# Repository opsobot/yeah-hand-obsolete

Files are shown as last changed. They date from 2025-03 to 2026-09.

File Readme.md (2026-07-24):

Yeah Hand (Rebelia V2) - An Open Source Robotic Hand for Humans and Robots
==========================================================================
**Official development partner: Public Invention** [Public Invention Project Page](https://www.pubinv.org/project/yeah-robotic-hand/)



**Original design by Vittorio Lumare** [Hackaday Project Page](https://hackaday.io/project/204373)

**Successor to OSHWA-certified [Rebelia V1](https://github.com/OPSOBOT/rebelia/tree/V1)**

Licenses: 
- CERN-OHL-S-2.0 (Hardware)
- GNU GPLV3 (Software)
- CC-BY-SA (Documentation)

Contributing
------------
- Original hardware, software and documentation by Vittorio Lumare
- Code contributions via Pull Requests to OPSOBOT/yeah-hand
- Public Invention: Official development partner
- All contributions under CERN-OHL-S-2.0 (Hardware), GNU GPL (Software), CC-BY-SA (Docs)

Overview
========

Welcome to the Yeah Hand Project — an open-source, humanlike robotic hand designed for researchers, students, and robotics enthusiasts.

Our goal is to provide an affordable, high-performance robotic hand under 2000 EUR, open to community contributions and continuous improvement.

NOTE: This version will be certified with OSHWA after is stable, at the moment the only version certified with OSHWA is the V1, you can check its branch 'V1' in the repo.

This project hardware is released under the CERN Open Hardware License (OHL-S), ensuring the design remains open-source and preventing patent claims on its core innovations.

The firmware is released under the GNU-GPL License.

The documentation is released under the CC-BY-SA License.

Features
* Fully 3D-printable design using affordable materials.
* Commercial off-the-shelf components for servos and electronics.
* Custom firmware for precise motor control.
* Modularity for easy upgrades and customization.

Our Approach to Open-Source Release
===================================
We use a copyleft open-source license to protect user freedoms and encourage meaningful collaboration, while maintaining a sustainable business model. Our strategy is as follows:

1. Development and Testing: We begin by developing and rigorously testing a new version of our product (including source code, CAD files, documentation, etc.) to ensure it meets our quality and performance standards.

2. Preparation for Launch and Sales: Once the new version is stable, we prepare it for market with dedicated marketing and pre-sales efforts. This phase ensures visibility and early adoption by our community and customers.

3. Open-Source Copyleft Release: We release each version immediately under a copyleft license (e.g., CERN-OHL, GPL), ensuring that the community can study, modify, and share the design—while also preserving those freedoms in derivative works. At the same time, we begin commercial distribution of that version.

4. Sustainable Sales and Ongoing Development: We continue to sell the open-source version for as long as it remains commercially viable, using the generated revenue to support our business, provide user support, and fund future development.

5. Continuous Innovation Cycle: While a version is being sold, we work on the next iteration—improving the design and preparing it for the next release. Once ready, we return to step 2, keeping the cycle of development, open-source release, and sustainable sales in motion.

This strategy ensures that we stay aligned with open-source ethics while securing the resources needed to support our work. It allows us to protect user freedom through copyleft, promote transparency, and build a strong, collaborative community—all while continuing to grow as a business.

Repository Structure
====================

```
/hardware
  ├── CAD/ (STL native Blender format)
    ├── LICENSE (CERN OHL-S)
  ├── renders/ (images of the robotic hand)
    ├── LICENSE (CC-BY-SA)
  ├── BOM.md (Bill of Materials — list of components and suppliers)
/firmware
  ├── LICENSE (GNU GPL)
  ├── src/ (firmware code)
  ├── README.md (how to compile and upload the firmware)
/docs
  ├── Assembly Instructions.odt (Original source document)
  ├── Assembly Instructions.pdf (Exported final document)
├── LICENSE (licenses description for the whole repo)
├── README.md (project overview)
```

CAD Files
=========

Our CAD files are hosted on both GitHub and GrabCAD:
* GitHub (for version control and collaboration): ./hardware/CAD folder
* GrabCAD (for easy preview and download): TODO when development is completed )

Bill of Materials (BOM)
=======================
Find the full list of commercial components required to build the robotic hand in BOM.md.

Firmware
========
The custom firmware is located in the /firmware directory. Instructions for compiling and uploading are available in the Firmware README.

Licensing
=========
This project is licensed under multiple licenses:
* Hardware : released under the CERN Open Hardware License Strongly Reciprocal v2 (CERN OHL-S). [Full license text](https://ohwr.org/project/cernohl/-/wikis/uploads/819d71bea3458f71fba6cf4fb0f2de6b/cern_ohl_s_v2.txt)
* Firmware : released under the GNU GPL License. [Full license text](https://www.gnu.org/licenses/gpl-3.0.html)
* Multimedia : released under the Creative Commons Attribution License (CC-BY-SA). [Full license text](https://creativecommons.org/licenses/by-sa/4.0/deed.en)

By using or modifying this hardware, software and/or documentation, you agree to:
* Credit the original authors.
* If you release any modifications or derivatives to hardware, they must be released under the same CERN OHL-S license.
* If you release any modifications or derivatives to firmware, they must be released under the same GNU GPL license.
* If you release any modifications or derivatives to multimedia content, they must be released under the same CC-BY-SA license.
* Prevent patent claims on the design and any derivative works.

Contributing
============
We welcome contributions! Please:
1. Fork the repo.
2. Create a branch (feature-xyz).
3. Submit a pull request.

Defensive Publication
=====================
This design is publicly released to establish prior art and prevent patenting by third parties. 
Our goal is to ensure that the robotic hand remains open and accessible to all.

For further information, visit our website: http://www.robotgarage.org

Contact
=======
For any questions or collaborations, reach out to us at: vittorio.lumare@robotgarage.org.

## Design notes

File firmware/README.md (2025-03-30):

Rebelia Hand Firmware
=====================

Overview
========

This folder contains the firmware for the Rebelia Hand, responsible for controlling the servomotors and processing commands for hand movements. The firmware is designed to work seamlessly with the open-source hardware of the robotic hand.

The firmware is licensed under the GNU GPL License, ensuring that any modifications or derivatives remain open-source and freely available to the community.

Structure
=========

```
/firmware
  ├── src/               # Source code for the firmware
  ├── include/           # Header files (.h)
  ├── LICENSE.txt        # Full text of the GPLv3 license
  ├── README.md          # This document
  └── Makefile           # Build instructions (optional, if applicable)
```

Licensing
=========

The firmware in this folder is released under the GNU GPL License.

By using or modifying this firmware, you agree to:

Attribute the original authors.

If you distribute any modified versions of this firmware, they must be released under the same GNU GPL license.

Include a copy of the GNU GPL license with any distribution of this firmware.

You can find the full license text in the LICENSE.txt file.

Copyright Notice
================

Each source file contains a copyright notice similar to the following:

```
/*
  Rebelia-Hand-Firmware is the control software for the Rebelia Hand

  Website: https://www.robotgarage.org
  Author: Vittorio Lumare
  Email: vittorio.lumar@robotgarage.org 

  GNU GPL License

  Copyright (c) 2025 Vittorio Lumare

  This file is part of Rebelia-Hand-Firmware.

  Rebelia-Hand-Firmware is free software: you can redistribute it and/or 
  modify it under the terms of the GNU General Public License as published 
  by the Free Software Foundation, either version 3 of the License, or 
  (at your option) any later version.

  Rebelia-Hand-Firmware is distributed in the hope that it will be useful, 
  but WITHOUT ANY WARRANTY; without even the implied warranty of 
  MERCHANTABILITY or FITNESS FOR A PARTICULAR PURPOSE. 
  
  See the GNU General Public License for more details.

  You should have received a copy of the GNU General Public License along 
  with Rebelia-Hand-Firmware. If not, see <https://www.gnu.org/licenses/>. 
*/
```

Dependencies
==================
This firmware may reference external libraries via `#include <library.h>`. These libraries are not included in this repository, and it is the user's responsibility to ensure they are installed and correctly licensed.

Please refer to the following external dependencies:

* SCServo by FT&WS: (GNU GPL) — [https://github.com/workloads/scservo]
* BluetoothSerial by Henry Abrahamsen: [Released into the public domain] — [https://github.com/hen1227/bluetooth-serial]
* ESP32FFT modified version by Vittorio Lumare: (Custom License) — [https://github.com/vittorio-lumare/ESP32FFT]
	* Note:  The original version is by Robin Scheibler [https://github.com/fakufaku/esp32-fft]

Prepare the Arduino IDE for ESP32
=================================
1. Install the Arduino IDE 2
2. Open the Arduino IDE 2
3. Open the Arduino Boards Manager
	1. Install 'esp32' by Expressif Systems

Install the Libraries
=====================
Note: Some libraries are manually installed, while others use Arduino's Library Manager. 

Libraries with manual installation
----------------------------------
1. Install the ESP32FFT library:
2. Download the ESP32FFT Arduino library from [https://github.com/vittorio-lumare/ESP32FFT]
3. Save the 'ESPfft' folder in your `Documents/Arduino/libraries` folder.

Libraries with automatic installation
-------------------------------------
1. Open Arduino IDE.
2. Go to Sketch → Include Library → Manage Libraries.
3. Open the Arduino's Library Manager:
	1. Search and install 'SCServo' by FT&WS
 	2. Search and install 'BluetoothSerial' by Henry Abrahamsen

Alternatively, you can manually install these libraries by downloading them and placing them in your `Documents/Arduino/libraries` folder.

Prepare the 'Rebelia Human' sketch
==================================
1. Open the Arduino IDE 2
2. Open 'RebeliaHuman' sketch

How to Compile and Upload
=========================
1. Ensure you have all dependencies installed.
2. Navigate to the firmware directory and open the .ino file using Arduino IDE.
3. Use Arduino IDE to build and upload the binary to the microcontroller board.

Contributions
=============
Contributions are welcome! To contribute:

1. Fork the repo.
2. Create a branch (feature-xyz).
3. Submit a pull request.

Contact
=======
For any questions or collaboration, reach out at vittorio.lumare@robotgarage.org
Please stay tuned on https://www.robotgarage.org
Feel free to open issues for bugs, feature requests, or discussions!

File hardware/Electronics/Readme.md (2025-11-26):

The prosthetic version uses a custom PCB, project files are in the 'Prosthetic Version' folder.

The robotic version uses a commercial board manufactured by WaveShare, the [ESP32 Servo Driver](https://www.waveshare.com/servo-driver-with-esp32.htm).

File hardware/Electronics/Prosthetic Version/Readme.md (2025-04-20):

Electronics Board - Prosthetic Version
======================================
This project was made using Osmond PCB.

The version used was OsmondCocoa 1.2.8 for MacOS.

Link: https://www.osmondpcb.com/

You can use the provided Netlist and Partlist files with any other software, to create your own version.

you can also just use the already exported gerber files and postscript files.

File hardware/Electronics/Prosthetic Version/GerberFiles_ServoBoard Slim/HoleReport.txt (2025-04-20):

Tool   Size   Count  Plated

 T1    0.0250     3     Yes
 T2    0.0276     2     Yes
 T3    0.0300     4     Yes
 T4    0.0350    27     Yes
 T5    0.0380     4     Yes
 T6    0.0400    39     Yes
 T7    0.0450     4     Yes
 T8    0.1250     1     Yes

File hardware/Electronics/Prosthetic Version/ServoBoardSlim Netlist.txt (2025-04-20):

Signal "Ground"
  { ICTX-3 ICRX-3 R21-2 C19-2 C20-2 CN5-3 CNPWR-1 CNEMG-1 CIN-2 COUT-2 D1-P IC2575-3 IC2575-5 ICESP32-17 ICESP32-14 }

Signal "Vcc3v3"
  { ICESP32-16 ICTX-5 ICRX-5 R24-1 R23-1 Q1-1 R19-1 C19-1 C20-1}

Signal "Vcc5v"
  { CNEMG-2 COUT-1 ICESP32-15 L1-2 IC2575-4 }

Signal "Vcc12v"
  { CNPWR-2 IC2575-1 CIN-1 CN5-2}

Signal "Output"
  { IC2575-2 D1-N L1-1 }

Signal "Q1Base" 
  { Q1-2 R20-1 }

Signal "R22toR21"
  { R22-2 R21-1 }

Signal "Tx"
  { R20-2 R24-2 R23-2 ICTX-2 ICESP32-25}

Signal "Rx"
  { ICRX-4 ICESP32-24 }

Signal "TxEn"
  { Q1-3 R22-1 ICTX-1 ICRX-1 }

Signal "Data"
  { ICTX-4 ICRX-2 R19-2 CN5-1 }

Signal "Emg1"
  { ICESP32-4 CNEMG-3}

Signal "Emg2"
  { ICESP32-5 CNEMG-4}

Signal "Emg3"
  { ICESP32-6 CNEMG-5}

Signal "Emg4"
  { ICESP32-7 CNEMG-6}

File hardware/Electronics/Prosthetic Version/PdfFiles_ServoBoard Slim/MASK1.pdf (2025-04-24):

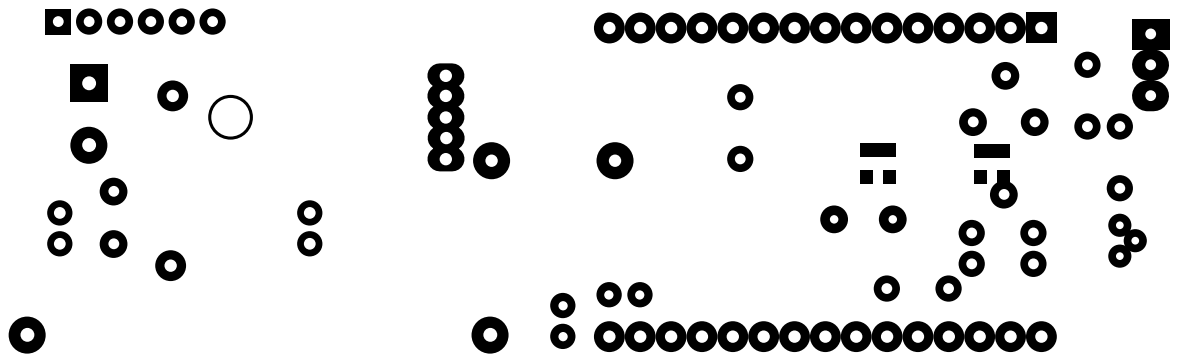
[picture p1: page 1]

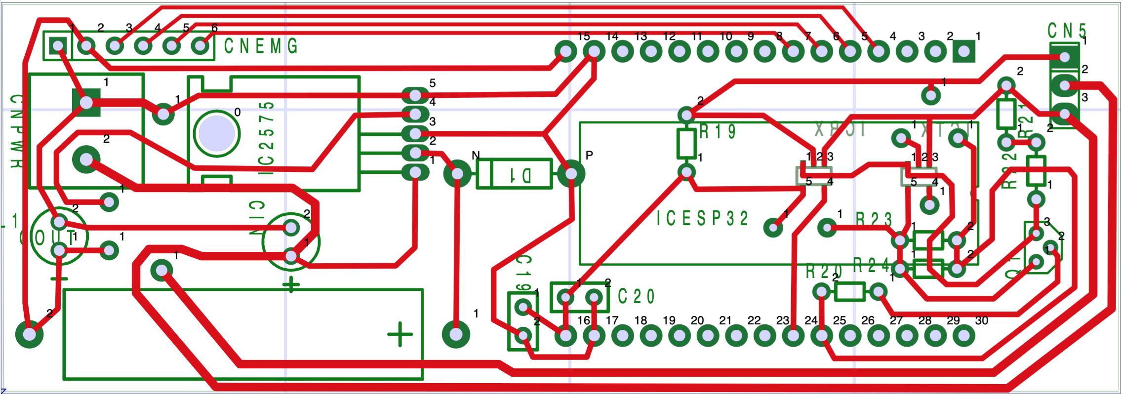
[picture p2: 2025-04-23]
hardware/Electronics/Prosthetic Version/ServoBoard Slim.png

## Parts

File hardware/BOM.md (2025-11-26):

Rebelia - An Open Source Robotic Hand for Humans and Robots
===========================================================

BOM
===
All components required to assemble Rebelia V2 are listed here.

Servomotors
===========
* 5 x WaveShare ST3215

Logic Board
===========
Robotic Version
---------------
* 1 x WaveShare - ESP32 Servo Driver

Prosthetic Version
-----------------

* Electronic Board Components
  * CAPACITORS: 
  	* CIN: 100uF/50V
  	* COUT: 330uF/16V
  	* C19: 100nF
  	* C20: 100nF
  * INDUCTORS: 
  	* L1: 330uH
  * DIODES: 
  	* D1: 1N5819
  * ICS: 
  	* IC2575: LM2575T−5G (5V, TO-220)
  	* ICESP32: ESP32-WROOM-32 30 Pin, Micro-USB
  	* ICRX: sn74lvc1g125
  	* ICTX: sn74lvc1g126
  * TRANSISTORS:
  	* Q1: SS8550 (TO-92A)
  * CONNECTORS: 
  	* CNPWR:
    * Alternatives:
     * KF128 5.08mm pitch, 2 Positions, PCB Screw Terminal Blocks Connector for Wires
     * Phoenix Contact MKDS 1,5/ 2-5,08 - PCB terminal block 
  	* CNEMG:
    * Alternatives
     * KF128 2.54mm pitch, 6 Positions, PCB Screw Terminal Blocks Connector for Wires
     * Phoenix Contact MPT 0,5/ 6-2,54 - PCB terminal block 
  	* CN5: MOLEX 90 DEG Mini SPOX 5268
  * RESISTORS:
  	* R19: 10k Ohm
  	* R20: 10k Ohm
  	* R21: 10k Ohm
  	* R22: 10k Ohm
  	* R23: 10k Ohm
  	* R24: 10k Ohm
* EMG Sensors
  * 2 x OyMotion EMG Sensor (https://www.oymotion.tech/OYMotion-EMG-Sensor-Analog-Output-Set-pd768341688.html) 

Tendons
=======
* 1 x Fish line : HERCULES 8 Braided Strands 200lbs, 0.75mm diameter, Grey
* 1 x PTFE Pipe OD:3mm, ID:1.5mm, Length 1m

Nuts and Bolts
==============
Hand part (from wrist to fingers) - Robotic and Prosthetic version
* Index, Middle, Ring and Little Fingers
  * 4 x M3 nuts, inox stainless steel
  * 4 x M3 bolts, 12mm length, hexagonal hole countersunk head, stainless steel
* Spools
  * 16 x M3 bolts, 10mm length, hexagonal hole button head, inox stainless steel (max head diameter 5.7mm)
* Servos
  * 20 x M2 self tapping screws, 8mm length, button head, inox stainless steel
* Palm
  * 7 x M2 self tapping screws, 10mm length
* Covers
  * 10 x M2 self tapping screws, 10mm length
* Wrist : TODO (M3)

Socket Part (from elbow to wrist) - Only Prosthetic version
* Socked door : 4 x M2 self tapping screws, 10mm length

3DP Filaments
=============
* Flexible Fingers: TPU + PLA/ABS
* Thumb Base: PLA/PETG
* Skeleton, Spools: ABS
* Covers: PLA

Silicone Pads
=============
* Smooth-On DragonSkin NV10 (https://www.smooth-on.com/products/dragon-skin-10-nv/)

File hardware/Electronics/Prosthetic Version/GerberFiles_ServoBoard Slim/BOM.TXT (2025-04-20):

1	1	1N4XXX		D1	
2	6	AXIAL0.2		R19	R20	R21	R22	R23	R24	
3	1	AXIAL1.50		L1	
4	1	DIP30-WIDE11		ICESP32	
5	2	DPV		ICRX	ICTX	
6	1	POWER2		CNPWR	
7	2	RAD0.1		C19	C20	
8	2	RB.1.2		CIN	COUT	
9	1	SIP3		CN5	
10	1	SIP6		CNEMG	
11	1	TO-220-5pin		IC2575	
12	1	TO-92A		Q1

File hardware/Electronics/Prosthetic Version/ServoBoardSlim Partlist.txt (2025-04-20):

Part DPV { Name ICTX }
Part DPV { Name ICRX }
Part SIP3 { Name CN5 }
Part POWER2 { Name CNPWR }
Part SIP6 { Name CNEMG }
Part AXIAL1.50 { Name L1 }
Part 1N4XXX { Name D1 }
Part TO-220-5pin { Name IC2575 }
Part RB.1.2 { Name CIN }
Part RB.1.2 { Name COUT }
Part RAD0.1 { Name C19 }
Part RAD0.1 { Name C20 }
Part AXIAL0.2 { Name R19 }
Part AXIAL0.2 { Name R20 }
Part AXIAL0.2 { Name R21 }
Part AXIAL0.2 { Name R22 }
Part AXIAL0.2 { Name R23 }
Part AXIAL0.2 { Name R24 }
Part TO-92A { Name Q1 }
Part DIP30-WIDE11 { Name ICESP32 }

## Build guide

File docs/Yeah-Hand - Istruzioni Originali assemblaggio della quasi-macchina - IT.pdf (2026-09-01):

Yeah Hand™ – Istruzioni per l’assemblaggio della quasi‑macchina Yeah Hand™ – Rev 1.7 – IT

Yeah Hand™ – Mano Robotica Elettrica Adattiva – © 2023-2026 Vittorio Lumare

# Istruzioni per l’assemblaggio della quasi‑macchina Yeah Hand™

## Manuale per l’integrazione, configurazione e uso da parte di integratori/assemblatori Istruzioni Originali

### Nome dell’ Azienda: VITTORIO-LUMARE

### Nome del Prodotto: VITTORIO-LUMARE Yeah Hand™

### Modello: Yeah Hand L / Yeah Hand R

### Tipo di Prodotto: Mano Robotica

### Prodotto in fase di sviluppo (prototipo / quasi-macchina) destinata

solo a integratori e beta tester, non a utenti finali.

### Indirizzo Fabbricante:

### Vittorio Lumare

### via Boccioni 4

### 88900 CROTONE (KR)

### Italy

### Revisioni

Version | Comment | Author | Date
1.0 | Versione Iniziale | Vittorio Lumare | 20/09/2024
1.0 - IT | Traduzione in Italiano | Fortunato Pantisano | 11/11/2025
1.1 - IT | Completamento traduzione (DOI) | Vittorio Lumare | 11/11/2025
1.2 - IT | Aggiornamento DOI e certificati | Vittorio Lumare | 11/11/2025
1.3 - IT | Aggiunto capitolo “Rischi residui da trasmettere agli utilizzatori” | Vittorio Lumare | 12/01/2026
1.4 - IT | Aggiornato assemblaggio | Vittorio Lumare | 24/06/2026
1.5 - IT | Rinominati termini, aggiunti termini al glossario, rimosse sezioni relative a componenti non piú facenti parte del prodotto, corretti errori nelle illustrazioni | Vittorio Lumare | 21/07/2026
1.6 – IT | Modificata procedura installazione tendine su spool dito pollice | Vittorio Lumare | 26/08/2026
1.7 – IT | Convertito documento da .odt a .docx per compatibilita con IA, molte figure rese statiche per stabilita di posizionamento | Vittorio Lumare | 27/08/2026

## 1 Avvertenze generali e conformità della macchina

## 1.1 Struttura del documento

## Indice

## 1.2 Modalita di consultazione

Invitiamo i lettori a leggere per primo il capitolo sulla sicurezza, che è l'aspetto più critico e importante.
In seguito è possibile saltare al capitolo desiderato, ognuna consultabile di per se, tenendo conto ogni capitolo fa riferimento agli altri con alcuni link, quindi è possibile consultare direttamente la sezione interessata.
Nel capitolo finale sono presenti le illustrazioni con la nomenclatura delle parti, che andranno consultate durante la procedura di assemblaggio.

## 1.3 Riferimenti legislativi

Direttive | Requisiti applicabili soddisfatti
Regolamento Macchine (UE) 2023/1230 | 1.1.2, 1.1.3, 1.1.5, 1.3.2, 1.3.3, 1.3.4, 1.3.8.1, 1.5.1, 1.5.2, 1.5.5, 1.5.6, 1.6.1, 1.7.1, 1.7.2, 1.7.4, 1.7.4.1, 1.7.4.2, 4.1.2.3, 4.1.2.4, 4.3.1, Annex VI. Si dichiara che la documentazione tecnica pertinente è stata compilata in conformità alla Parte B dell'Allegato IV del Regolamento Macchine. Il fabbricante si impegna a trasmettere, su richiesta delle autorità nazionali, la documentazione tecnica pertinente specificata nell'Allegato IV, Parte B, entro i termini richiesti.
2014/30/EU Direttiva sulla compatibilità elettromagnetica (EMC) | Fare riferimento alla direttiva EMC e agli standard armonizzati utilizzati di seguito.
2011/65/EU Restrizione dell'uso di determinate sostanze pericolose (ROHS) | Fare riferimento alla direttiva ROHS e agli standard armonizzati utilizzati di seguito.
STANDARD INTERNAZIONALE | DESCRIZIONE
EN ISO 12100:2010 | 2012 Sicurezza della Macchina — Principi generali di progettazione — Valutazione e riduzione del rischio
EN 60204-1 | 2009 Sicurezza della Macchina – Equipaggiamento elettrico della macchina – Parte 1: Requisiti generali
ISO 14539:2000 | Manipolazione di robot industriali — Manipolazione di oggetti con pinze di tipo grasping — Vocabolario e presentazione delle caratteristiche
ISO 14121-2 | ISO/TR Sicurezza della Macchina – Valutazione dei rischi – Parte 2: Guida pratica ed esempi di metodi

## 1.4 Bozza della Dichiarazione UE di Incorporazione

Bozza della Dichiarazione UE di Incorporazione Originale

Ai sensi del Regolamento (UE) 2023/1230, Allegato V, Parte B, del Parlamento Europeo e del Consiglio, relativa alle macchine,

Noi, il fabbricante,

VITTORIO-LUMARE
via Boccioni 4, 88900 CROTONE (KR) - Italy

Con la presente dichiariamo che il seguente prodotto:

Nome Prodotto: VITTORIO-LUMARE Yeah Hand

Descrizione: Mano Robotica Umanoide

Funzioni: Manipolazione di oggetti, Pick and Place, gesti.

Modelli: Yeah Hand L, Yeah Hand R

Tipi: Mano Robotica Elettrica Adattiva

Serial number:

La quasi‑macchina oggetto della presente dichiarazione non può essere messa in servizio prima che sia stata confermata la conformità della macchina, in cui la quasi-macchina deve essere incorporata, alle disposizioni del Regolamento Macchine. La conformità a tutti i requisiti essenziali del Regolamento Macchine dipende dalla specifica applicazione robotica e dalla complessiva valutazione del rischio.

Direttive / Regolamenti | Requisiti applicabili soddisfatti
Regolamento UE Macchine 2023/1230 | 1.1.2, 1.1.3, 1.1.5, 1.3.2, 1.3.3, 1.3.4, 1.3.8.1, 1.5.1, 1.5.2, 1.5.5, 1.5.6, 1.6.1, 1.7.1, 1.7.2, 1.7.4, 1.7.4.1, 1.7.4.2, 4.1.2.3, 4.1.2.4, 4.3.1, Annex VI. Si dichiara che la documentazione tecnica pertinente è stata compilata in conformità alla conformità alla Parte B dell'Allegato IV del Regolamento Macchine. Il fabbricante si impegna a trasmettere, su richiesta delle autorità nazionali, la documentazione tecnica pertinente specificata nell'Allegato IV, Parte B, entro i termini richiesti.
2014/30/EU Direttiva sulla compatibilità elettromagnetica (EMC) | Fare riferimento alla direttiva EMC e agli standard armonizzati utilizzati di seguito.
2011/65/EU Restrizione dell'uso di determinate sostanze pericolose (ROHS) | Fare riferimento alla direttiva ROHS e agli standard armonizzati utilizzati di seguito.

Responsabile della Documentazione: Vittorio Lumare. Indirizzo: vedere l'indirizzo del fabbricante.

CROTONE, 07/09/2024 (luogo e data di emissione)

Vittorio Lumare – Direttore Tecnico

VITTORIO-LUMARE

Sono stati applicati i seguenti standard:

STANDARD INTERNAZIONALE | DESCRIZIONE
EN ISO 12100:2010 | 2012 Sicurezza della Macchina — Principi generali di progettazione — Valutazione e riduzione del rischio
EN 60204-1 | 2009 Sicurezza della Macchina – Equipaggiamento elettrico della macchina – Parte 1: Requisiti generali
ISO 14539:2000 | Manipolazione di robot industriali — Manipolazione di oggetti con pinze di tipo grasping — Vocabolario e presentazione delle caratteristiche

ISO 14121-2 | ISO/TR Sicurezza della Macchina – Valutazione dei rischi – Parte 2: Guida pratica ed esempi di metodi

## 1.5 Prodotti incorporati

Prodotti incorporati
- 5 Servomotori
- Fabbricante: Shenzhen Waveshare Electronics Co., Ltd
- Modelli: ST3215 Servo, ST3215-HS Servo Motor
- Scheda elettronica di controllo
- Fabbricante: Shenzhen Waveshare Electronics Co., Ltd
- Modello: Servo Driver with ESP32

Figure 1.1: WaveShare
Servomotor ST3215-HS

Figure 1.2:
WaveShare ESP32
Servo Driver

## 1.6 Targhetta prototipo / pre-serie

La targhetta definitiva, comprensiva di eventuale marchio, verrà aggiornata nella versione finale del prodotto.

## TO DO INSERIRE LOGO Produttore: VITTORIO-LUMARE

## Modello: YEAH-HAND-L / YEAH-HAND-R TBD SN: 2026 000000 Anno: 2026

## 2 Sicurezza

## 2.1 Avvertenze Inerenti situazioni pericolose

2.1.1 Significato simboli
Questo paragrafo spiega il significato dei simboli usati nel resto del manuale.
Si prega di leggere e comprendere in questo capitolo il significato di ogni simbolo.

LEGGERE IL MANUALE DI ISTRUZIONI

OBBLIGO DI USARE LA MORSA

OBBLIGO DI USARE LA PINZA MANUALE DI MONTAGGIO

NON SPRUZZARE LIQUIDI SULLA MANO ROBOTICA

PERICOLO DI TAGLIO DITA DA CAVI

PERICOLO CADUTA OGGETTI DALL'ALTO

PERICOLO PROIEZIONE OGGETTI

PERICOLO DI INCENDIO

PERICOLO DI SUPERFICI CALDE

PERICOLO DI TAGLIO PARTI DEL CORPO

PERICOLO DI SCHIACCIAMENTO PARTI DEL CORPO

PERICOLO DI SOSTANZE DANNOSE PER LA SALUTE

PERICOLO ELETTRICITÀ

2.1.2 Operazioni di manutenzione

!! NON TIRARE I TENDINI A MANI NUDE !!

OBBLIGATORIO
- Usare una morsa per tenere ferma la parte su cui operare
- | Usare una pinza manuale di montaggio per | tirare i tendini
POSSIBILI DANNI:
- Gravi tagli alle dita
- Dissanguamento che richiede immediato intervento chirurgico

2.1.3 Messa in servizio
PRIMA DELLA MESSA IN SERVIZIO DELLA MACCHINA COMPLETA CHE INTEGRERÀ LA MANO ROBOTICA, I SEGUENTI SIMBOLI VANNO APPLICATI SUL PRODOTTO FINALE, IN MODO CHE SIANO SEMPRE VISIBILI A POSSIBILI PERSONE NELLE VICINANZE

2.1.4 Funzionamento tipico
2.1.4.1 Persone vicine alla mano robotica

ATTENZIONE: la mano robotica potrebbe rompersi durante l'uso!
DANNI POSSIBILI: Se la mano robotica si rompe, alcune parti rotte potrebbero essere affilate o appuntite e potrebbero tagliare la pelle delle persone e causare danni permanenti o dissanguamento e/o richiedere un intervento chirurgico immediato

2.1.4.2 Mano robotica che tiene un oggetto

ATTENZIONE: un oggetto potrebbe staccarsi dalla mano robotica e colpire una persona
DANNI POSSIBILI: Un oggetto lanciato potrebbe causare: rottura di ossa, tagli o infilzamento, bruciature se è molto caldo, contaminazione se contiene o è composto da sostanze nocive.

2.1.4.3 Interazione con persone

ATTENZIONE: le dita o la pelle umana possono rimanere incastrate nei meccanismi e ferirsi POSSIBILI DANNI: un dito può essere schiacciato fino a causare gravi contusioni alla pelle o alle unghie, un tendine può tagliare un dito umano fino a causare dissanguamento e/o richiedere un intervento chirurgico immediato, parti taglienti possono tagliare la pelle causando fuoriuscite di sangue o lividi.

2.1.5 Situazioni di rischio e rischi residui

Situazione Pericolosa | Evento Pericoloso | Pericolo | RISCHI RESIDUI DOPO L'IMPLEMENTAZIONE DELLE MISURE DI RIDUZIONE
Manipolazione dei fili dei tendini | Contatto delle dita umane con il tendine tirato con forza | Taglio o abrasione delle dita umane da parte dei fili dei tendini | Lesioni cutanee se l'operatore non segue le istruzioni durante: • • la rimozione/inserimento del tendine

2.1.6 Uso consentito della macchina e rischi residui

Situazione Pericolosa (ISO 12100:2010, Tabella B.3) | Evento Pericoloso (ISO 12100:2010, Tabella B.4) | Pericolo (ISO 12100:2010, Tabella B.1) | RISCHI RESIDUI DOPO L'IMPLEMENTAZIONE DELLE MISURE DI RIDUZIONE
Essere vicino all'area di lavoro della mano robotica (dipende dalla macchina completa che integra la mano robotica) | Rottura della mano robotica durante il funzionamento, con esposizione di parti taglienti o abrasive | Impatto, puntura, coltellata, abrasione | Sulla macchina completa, che integra la mano robotica, prodotta da altri, è possibile uno di questi rischi: • Una parte rotta può essere tagliente e tagliare la pelle umana fino a far fuoriuscire sangue e richiedere un intervento chirurgico immediato.
Essere a distanza sufficiente per essere colpito da un oggetto tenuto dalla mano robotica nel caso in cui l'oggetto si stacchi dalla mano robotica per qualsiasi motivo | Contatto con un oggetto che viene espulso/lanciato dalla mano robotica | Impatto, abrasione, taglio, pugnalata, puntura, ustione, elettrocuzione o contaminazione da sostanze pericolose causata da un oggetto espulso/lanciato | Sulla macchina completa, che integra la mano robotica, prodotta da altri, è possibile uno di questi rischi: • Un oggetto lanciato può causare: fratture ossee, tagli o ferite da taglio se taglienti, ustioni se calde, contaminazione se contengono o sono fatte di sostanze nocive.
Utilizzo intensivo della mano robotica | Fiamma generata da motori surriscaldati o scheda elettronica | Fiamma | Sulla macchina completa, che integra la mano robotica, prodotta da altri, è possibile uno dei seguenti rischi: • La mano robotica può incendiarsi se utilizzata intensamente oltre i suoi limiti.

2.1.7 Uso non consentito della macchina e rischi residui
Durante l'uso consentito della mano robotica, una volta integrato nella macchina finale, si possono verificare queste situazioni pericolose:
Situatione Pericolosa | Evento Pericoloso | Pericolo | RISCHI RESIDUI DOPO L'IMPLEMENTAZIONE DELLE MISURE DI RIDUZIONE
Essere vicino all'area di lavoro della mano robotica (dipende dalla macchina completa che integra la mano robotica) | Contatto con parti dannose dell'oggetto impugnato: spigoli vivi, punte, superfici abrasive | Puntura, coltellata, abrasione, ustione, elettrocuzione | Puntura, coltellata, abrasione, ustione, elettrocuzione
Essere vicino all'area di lavoro della mano robotica (dipende dalla macchina completa che integra la mano robotica) | Contatto con un oggetto pesante | Impatto | Impatto
Essere vicino all'area di lavoro della mano robotica (dipende dalla macchina completa che integra la mano robotica) | Contatto con la parte ad alta temperatura dell'oggetto tenuto in mano | Ustioni | Ustioni
Essere vicino all'area di lavoro della mano robotica (dipende dalla macchina completa che integra la mano robotica) | Contatto con la parte ad alta tensione dell'oggetto tenuto in mano | Elettrocuzione, ustione | Elettrocuzione, ustione
Essere vicino all'area di lavoro della mano robotica (dipende dalla macchina completa che integra la mano robotica) | Contatto con un oggetto tenuto contaminato da sostanze pericolose | Contaminazione da parte di sostanze pericolose di parte dell'oggetto custodito | Contaminazione da parte di sostanze pericolose di parte dell'oggetto custodito

É importante che gli integratori riducano le suddette situazioni di rischio, in quanto esse dipendono dalla macchina finale e i rischi collegati non possono essere ridotti agendo unicamente sulla mano robotica.

Le seguenti situazioni pericolose sono state analizzate e i relativi rischi sono stati ridotti dal fabbricante, esse presentano tuttavia ancora dei rischi residui.

Situazione Pericolosa (ISO 12100:2010, Tabella B.3) | Evento Pericoloso (ISO 12100:2010, Tabella B.4) | Pericolo (ISO 12100:2010, Tabella B.1) | RISCHI RESIDUI DOPO L'IMPLEMENTAZIONE DELLE MISURE DI RIDUZIONE
Toccare le falangi della mano robotica con le dita umane | Contatto delle dita umane con le parti mobili della mano robotica | Schiacciamento di dita umane molto piccole nello spazio tra il dito robotico e il tendine, taglio delle dita umane mediante trazione del tendine con forza | Sulla macchina completa, che integra la mano robotica, prodotta da altri, è possibile uno di questi rischi: • Il dito può essere compresso fino a causare gravi contusioni alla pelle o alle unghie • Il tendine può tagliare il dito umano fino a far fuoriuscire sangue e richiedere un intervento chirurgico
Toccare il palmo della mano robotica | Contatto delle dita umane con le parti mobili della mano robotica | Schiacciamento delle dita umane o della pelle nello spazio tra la base del pollice e il palmo o lo scheletro | Sulla macchina completa, che integra la mano robotica, prodotta da altri, è possibile uno di questi rischi: • Il dito può essere compresso fino a causare gravi contusioni alla

| | | pelle o alle unghie
Essere sotto la mano robotica quando si tiene un oggetto | Caduta di oggetti | Impatto di un oggetto che cade | Sulla macchina completa, che integra la mano robotica, prodotta da altri, è possibile uno di questi rischi: • Un oggetto che cade può causare: rottura ossea, tagli o coltellate se taglienti, ustioni se calde, contaminazione se contaminate
Toccare una mano robotica surriscaldato | Ustione causata dal contatto con la fiamma generata dalla mano robotica o dalla mano robotica surriscaldato | Ustioni | Sulla macchina completa, che integra la mano robotica, prodotta da altri, è possibile uno di questi rischi: • Ustioni cutanee causate dalle fiamme
Trovarsi a una distanza sufficiente da una mano robotica danneggiata per essere colpiti da un oggetto trattenuto dalla mano robotica danneggiata nel caso in cui l'oggetto si stacchi dalla mano robotica danneggiata per qualsiasi motivo | Contatto con un oggetto espulso/lanciato dalla mano robotica danneggiata | Impatto, abrasione, taglio, pugnalata, puntura, ustione, elettrocuzione o contaminazione da sostanze pericolose da parte di un oggetto espulso/lanciato | Sulla macchina completa, che integra la mano robotica, prodotta da altri, è possibile uno di questi rischi: • Un oggetto che cade può causare: fratture ossee, tagli o ferite da taglio se taglienti, ustioni se calde, contaminazione se contaminate. • Un oggetto lanciato può causare: fratture ossee, tagli o ferite da taglio se taglienti, ustioni se calde, contaminazione se contiene o è composto da sostanze nocive. • Una parte rotta può essere tagliente e tagliare la pelle umana fino a far fuoriuscire sangue e richiedere un intervento chirurgico immediato.

## 2.2 Dispositivi di protezione individuali

2.2.1 Dispositivi di protezione per assemblaggio e manutenzione

Durante le fasi di assemblaggio e manutenzione, è obbligatorio utilizzare i seguenti strumenti:
- Pinza manuale di montaggio per tenere e tirare i tendini
- Morsa per tenere ferma la mano robotica durante l'operazione

2.2.2 Dispositivi di protezione per uso consentito
Durante l'uso consentito della mano robotica, non sono necessari particolari dispositivi di protezione.
E' cura degli integratori analizzare ulteriori situazioni di rischio durante l'uso della macchina completa, e aggiungere e ventuali dispositivi di protezione appropriati.

## 2.3 Targhe di avvertimento applicate alla macchina

Questi simboli vanno applicati sulla macchina completa in modo che siano visibili agli operatori della macchina:

Questi simboli devono essere applicati sulla macchina completa prima della messa in servizio, in modo visibile a chiunque sia nel raggio d'azione della macchina completa a chiunque, operatori o semplici passanti o visitatori :

Questi simbolo deve essere applicati sulla macchina completa prima della messa in servizio, in modo visibile a chiunque sia nel raggio d'azione della macchina completa a chiunque, operatori o semplici passanti o visitatori, solo nel caso che la macchina completa che integra la mano robotica venga usata per manipolare oggetti contenenti sostanze pericolose per la salute

## 2.4 Situazioni di emergenza

In caso di fuoco, staccare l'alimentazione.
In caso di contaminazione da sostanze pericolose, gli integratori che hanno fabbricato la macchina completa che manipola tali sostanze, devono effettuare un'analisi dei rischi e valutare le situazioni di emergenza e scriverle nel technical file e nelle istruzioni della macchina completa.

## 3 Panoramica della macchina

## 3.1 Descrizione della macchina

Fabbricante | VITTORIO-LUMARE
Tipo di Macchinario | Mano Robotica (QUASI MACCHINA)
Modello Mano | Yeah Hand L (Mano Sinistra), Yeah Hand R (Mano Destra) Il modello del lato sinistro ricorda la mano umana "sinistra". Il modello del lato destro ricorda la mano umana "destra".
Tipo di mano robotica | Mano Robotica Elettrica Adattiva
Applicazioni principali della mano robotica | Robotica di servizio: • Afferrare/rilasciare oggetti • Scegli e posiziona • Utilizzo dei comandi del pannello • Utilizzo dei pulsanti meccanici • Gesti delle mani per le interazioni con i robot umani

Overall Technical Drawing - External View

Detailed Technical Drawing - Internal View

Detailed Technical Drawing - Measures

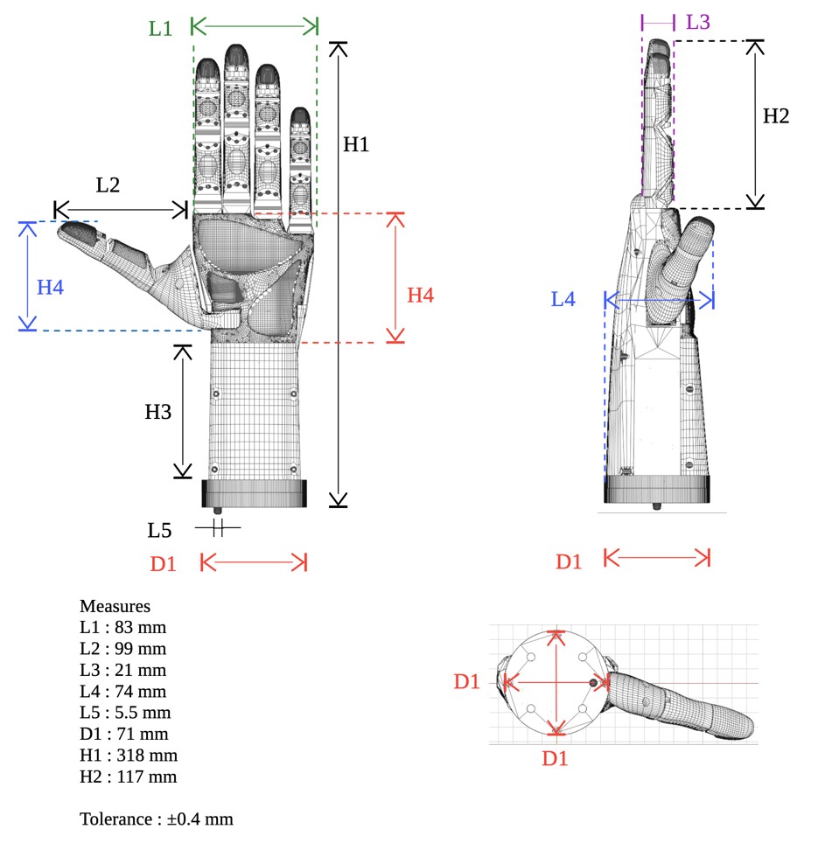
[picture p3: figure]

Detailed Technical Drawing

Detailed Technical Drawing

Detailed Technical Drawing

Detailed Technical Drawing

## 3.2 Uso previsto

Questa mano robotica elettrico è adattativa ed è pensata per applicazioni robotiche.
La mano robotica va installata su un dispositivo di movimentazione, come ad esempio:
- una piattaforma mobile
- un manipolatore robotico
- un robot di servizio umanoide
- un robot di servizio non umanoide

La mano robotica è adatta ad applicazioni:
- educative:
- scuole
- università
- ricerca:
- laboratori
- centri di ricerca
- università
- prototipazione:
- sviluppo di robot di servizio (umanoidi o meno) che integrano la mano robotica
- commerciali
- integrato in robot di servizio:
- in aree pubbliche
- per uso domestico
- hobbystiche

La mano robotica non è adatto ad applicazioni industriali, i quanto non possiede sufficienti:
- robustezza
- ripetibilità
- alta immunità ai disturbi tipici dell'ambiente industriale

## 3.3 Uso scorretto ragionevolmente prevedibile

Situazioni di uso scorretto:
- entrare in contatto fisico con esseri viventi
- manipolazione di pelle o parti del corpo
- stringere la mano di persone o animali
- ambiente altamente umido o con presenza di gocce d'acqua o vapori ad alta densità
- temperature oltre i 50 ˚C
- sollevare oggetti più pesanti di 2kg
- maneggiare sostanze pericolose per la salute, radioattive, altamente calde (oltre 50 gradi)
- maneggiare liquidi o sostanze polverose o con particelle piccole (inferiori a 12 mm)

## 3.4 Caratteristiche Tecniche della macchina

Prestazione della mano robotica
Massa della mano robotica (kg) | 650g senza coperture / 750g con coperture
Distanza Massima fra le dita (mm) | 160 mm
Distanza Minima fra le dita (mm) | 0
Forza di presa massima (N) | 90N (TBD : calculated)
Forza di manipolazione massima (N) | 35N (TBD : calculated)
Momento massimo ammissibile del dito (N*m) | 0.1
Superficie di presa (mm² ) | 1260
Tempo di funzionamento: Presa (s) | 2
Tempo di funzionamento: Rilascio (s) | 2

Tipo di mano robotica
Numero di Dita | 5
Disposizione delle dita | Umanoide
Gradi di mobilità della mano robotica (4.3.1) | Presa spaziale: 6
Gradi di libertà della mano robotica (4.3.2) | 5
Tipo di presa (4.3.6) | 4.3.6.2 presa non centrica 4.3.6.3 presa adattiva 4.3.6.5 presa asimmetrica 4.3.6.6 forza della presa

Dita
Gradi di mobilità del dito (4.4.1) | Indice: 3 Medio: 3 Anulare: 3 Mignolo: 3 Pollice: 5
Gradi di libertà del dito (4.4.2) | Indice: 1 Medio: 1 Anulare + Mignolo: 1 Pollice: 2
Movimento dito (4.4.3) | • Indice: ◦ dita multi-articolari (4.4.3.3) ◦ dita meccanicamente indipendenti (4.4.3.6) • Medio: ◦ dita multi-articolari (4.4.3.3) ◦ dita meccanicamente indipendenti (4.4.3.6) • Anulare: ◦ dito multi-articolato (4.4.3.3) ◦ dito meccanicamente interconnesso (4.4.3.6) • Mignolo: ◦ dito multi-articolato (4.4.3.3) ◦ dito meccanicamente interconnesso (4.4.3.6) • Pollice: ◦ dita multi-articolari (4.4.3.3) ◦ dita meccanicamente indipendenti (4.4.3.6)

Attuatori (4.2.1.4)
Tipo di attuatori | Motori elettrici
Numero di attuatori | 5
Potenza nominale dell'attuatore (W) | 60W

Meccanismi di trasmissione di potenza (4.2.1.5)
Meccanismo Dita Superiori (indice, medio, anulare, mignolo) | Ingranaggio + cavo
Meccanismo di flessione del pollice | Ingranaggio + cavo
Meccanismo di rotazione del pollice | Ingranaggio
Nota: "cavo" è il tendine, è una lenza da pesca intrecciata in polietilene

Dettagli del movimento delle dita (in riferimento al sistema di coordinate dell'interfaccia meccanica come definito nella norma ISO 9787):
Definizione TCP (3.3.8): Offset dal piano XmYm | Zoffset = 146.1 mm
Definizione TCP (3.3.8): Offset dall'asse Zm | Xoffset = -0.1 mm Yoffset = 18.9 mm

Controllo Dita
Schema di controllo delle dita (4.5) | 4.5.6 Controllo Ibrido
Segnali di controllo | Comandi dei caratteri seriali wireless (BT, WiFi) • Signal 1 : Seleziona Modalitá ◦ Installazione dei Tendini ◦ Calibrazione dei Tendini ◦ Rilassamento (nessun movimento) ◦ Controllo della presa (POWER, POWERSMALL, MONKEY, PINCH) ◦ Controllo RAW (controllo completo di ogni articolazione delle dita) • Signale 2: ◦ Chiuso/Aperto Dita: 0-100 %
Segnali di feedback | Caratteri seriali wireless (BT, WiFi) • Posizione: valore intero • Velocità: valore intero • Carico: valore intero • Temperatura: valore intero • Corrente: valore intero • Movimento: valore intero (0: falso, 1: vero) • Stato: valore intero

Diagramma a blocchi del controllo dita

Funzioni di rilevamento (3.4)
Rilevamento della posizione | Si: Risoluzione: 4096, Range: [0, 360] gradi
Rilevamento Torque (Coppia) | Si: Risoluzione: 2000, Range: [-25, 25] Kg*cm
Rilevamento della Temperatura | Si: Precisione: 1˚C, Range: [0, 70]˚C
Rilevamento della Tensione | Si: Precisione: 0.1V, Range: [0, 12]V
Rilevamento della Corrente | Si (TBD)
Rilevamento del movimento | Valore: 1: Movimento, 0: Costante

Elementi di serraggio (4.6)
Materiale | • Polimero rigido (es. ABS / PLA / PETG / nylon) • Polimero flessibile (es. TPU / TPE) • Silicone sicuro per la pelle (es. Smooth‑On Dragon Skin NV / Reschimica R PRO GLASS)
Sostituibile | Si
Intercambiabile | Si

Ambiente operativo
Intervallo di temperatura | 10 – 40 ˚C
Intervallo di umidità relativa | 0 – 80 %
Protezione IP | IP20 (INSUFFICIENTE, DEVE ESSERE >IP4X)

pu : posizione desiderata dall'utente
pin : posizione comandata dal controllore C pout : posizione reale in uscita
lout : carico reale in uscita
C : Controllore principale della pinza
SCL: Anello di controllo del servomotore (interno al servomotore)

Proprietà dell'oggetto
Geometria (forma, dimensioni) (mm) | Forma: Qualsiasi forma Dimensioni: diametro massimo 10 cm
Massa dell'oggetto (kg) | 0 - 2 kg TBD
Temperatura massima/minima dell'oggetto (˚C) | 10˚C - 40˚C
Caratteristiche della superficie | Tutto ciò che non presenta: bordi/punte taglienti, superfici abrasive, sostanze nocive, liquidi, materiali radioattivi
Proprietà magnetiche | < 1T

Interfacce robotiche (4.7) e meccanismi del polso:
Interfaccia meccanica | Conforme allo standard | UNI EN ISO 9409-1:2005
| Codice di designazione | ISO 9409-1-50-4-M6
Funzionalità (trasmissione di energia e segnali) | Trasmissione di energia: corrente continua 12 V, max 14 A Nessuna trasmissione di segnali tramite l'interfaccia del robot (la trasmissione è wireless)

Avvertimento
Rischio (nella macchina finale) di: schiacciamento, puntura, taglio, pugnalata, incendio, ustione

## 3.5 Comandi e segnalazioni

La mano robotica non include comandi fisici, è dotato di un'interfaccia wireless seriale BlueTooth a caratteri.
L'implementazione di eventuali comandi è a carico degli integratori della macchina completa.

## 3.6 Limiti ambientali della macchina

Ambiente operativo
Intervallo di temperatura | 10 – 40 ˚C
Intervallo di umidità relativa | 0 - 80
Protezione IP | TBD: IP40

## 4 Trasporto, movimentazione immagazzinamento

## 4.1 Trasporto

La mano robotica può essere trasportato a mano.
Si consiglia di trasportare la mano robotica in un imballaggio che impedisca:
| • l'urto con superfici che possano compromettere l'integrita strutturale o la finitura delle superfici esterne. • l'infiltrazione di liquidi o polveri o materiali con dimensione inferiore a 12 mm TBD

Si consiglia di smontare la mano robotica dalla macchina su cui è integrato, se essa viene trasportata, in quanto potrebbe danneggiarsi durante il trasporto.
Durante il trasporto non deve essere superata la temperatura di 70 ˚C, altrimenti potrebbero verificarsi alterazioni geometriche dei materiali di cui é composto.
IMPORTANTE: Prima di trasportare la mano robotica, scollegare l'alimentazione!

## 4.2 Movimentazione

Si consiglia di utilizzare un manipolatore robotico per movimentare la mano robotica.

## 4.3 Immagazzinamento

La mano robotica può essere immagazzinato in queste condizioni:
| • temperatura ◦ 5˚C - 40˚C • umidità : ◦ 0 - 70% RH • luce: ◦ conservcare al buio in una scatola chiusa ◦ non esporre a raggi UV

## 5 Assemblaggio

Queste istruzioni spiegano come assemblare la mano robotica a partire dai suoi componenti già fabbricati.

## 5.1 Installazione e registrazione servomotori

Questa sezione descrive come installare i servomotori nello scheletro della mano e come registrarli sulla scheda logica per garantirne il corretto funzionamento.
Le procedure sono destinate a utenti adulti con competenze di base in elettronica e montaggio meccanico.

Figure 5.1: Mano Sinistra - Scheletro -Vista Posteriore – nessun componente montato

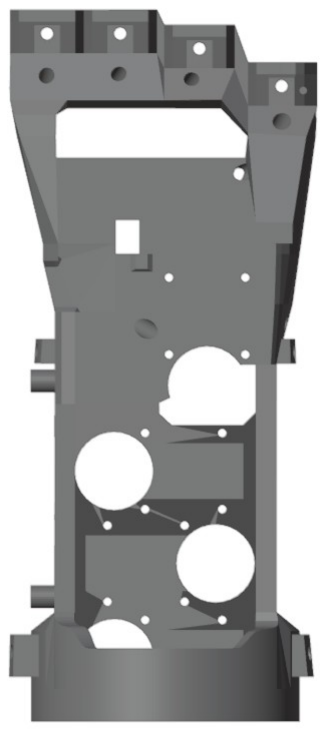
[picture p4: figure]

Figure 5.2: Mano Sinistra - Scheletro -Vista Anteriore – nessun componente montato

5.1.1 Installazione Base Pollice e servomotore Thumb Rotation (20 min) Nota: TRS è un acronimo di Thumb Rotation Servo
Installazione:
1. Installare Thumb Base sulla flangia del TRS (4 bulloni M3 lunghi 16 mm) come da figura 5.3.
2. Installare TRS sulla TRS Platform come mostrato in figura 5.4 e avvitare con 4 viti autofilettanti M3, lunghe max 6 mm (NON usare viti piu lunghe altrimenti si rompe il servomotore)
3. Inserire l'assemblato TRS Platform+Base Pollice sullo scheletro come mostrato in figura 5.5 e avvitare con 4 bulloni M2, lunghi 5 mm.

Figure 5.3: Thumb Base on the Thumb Rotation Servomotor

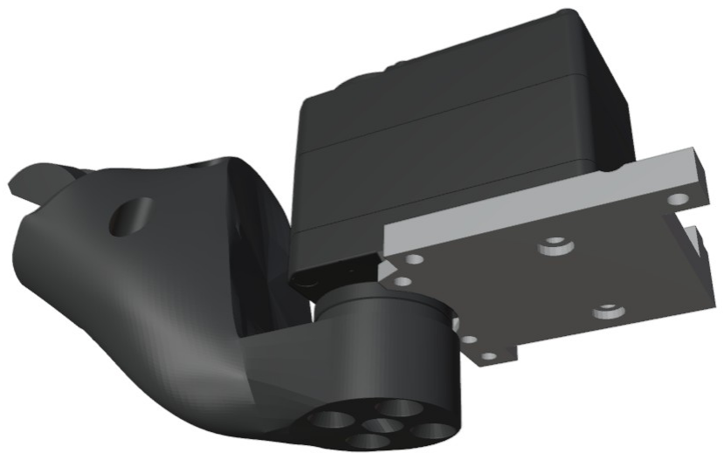
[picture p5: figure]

Figure 5.4: Thumb Base and TRS on TRS Platform

Figure 5.5: TRS e TRS Platform installati sullo scheletro

5.1.2 Installazione 4 servomotori per flessione dita (15 min)
Nota: ogni servomotore di flessione (ce ne sono 4) va fissato nel suo slot usando 4 viti autofilettanti M2 lunghe 6-8 mm.
1. Installare ogni servomotore nel relativo slot come mostrato nelle figure 5.5 e 5.6
2. Avvitare il servomotore ai fori dello scheletro usando le quattro viti fornite.
3. ATTENZIONE: Usare il cacciavite fornito e stringere leggermente le viti per evitare di danneggiare la sede filettata del servomotore, che è molto delicata.
1. Nota per il servomotore più in basso (quello alla base dello scheletro):
1. rimuovere la vite centrale della flagia rotante per permettere l'inserimento nello slot.
2. collegare al servomotore 2 cavi di controllo, in quanto successivamente non sara possibile inserirli.
3. Inserire il servomotore nello slot
4. Ri-avvitare la vite centrale sulla flangia.
4. Assicurarsi che tutti i cavi di controllo dei servomotori siano scollegati tranne quelli del servo piu in basso.

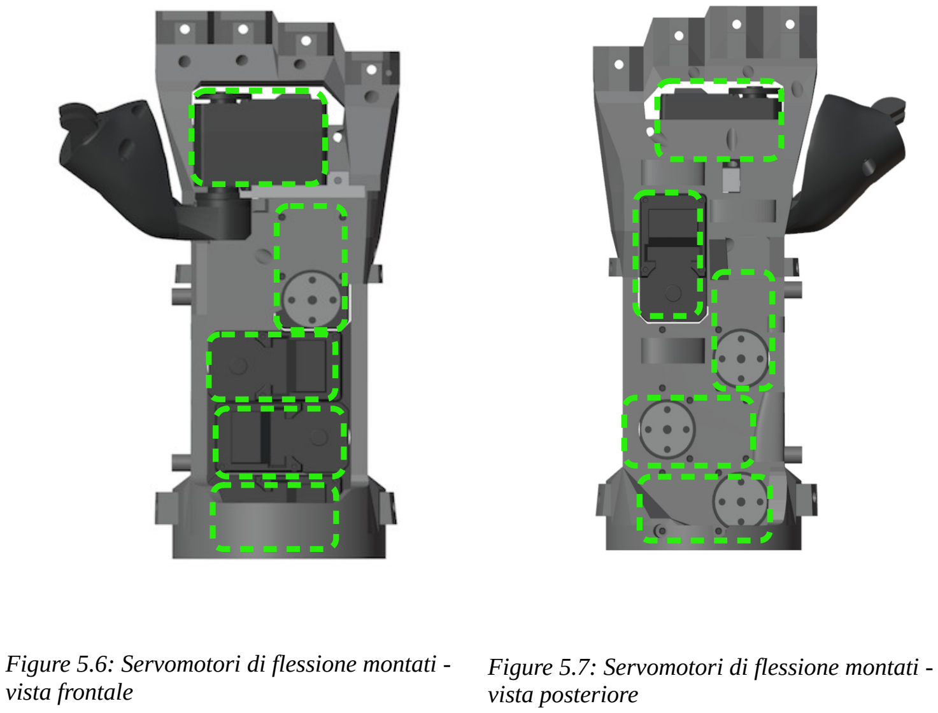
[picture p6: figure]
vista frontale; vista posteriore

Figure 5.6: Servomotori di flessione montati -Figure 5.7: Servomotori di flessione montati -

5.1.3 Registrazione e calibrazione servomotori

Prima di iniziare:
- Assicurati che la scheda logica sia
- smontata dalla mano
- spenta e scollegata sia dall’alimentatore che dal cavo USB.
- Scollega tutti i servomotori dalla scheda logica.

Procedura (per ogni servomotore di flessione):
1. Collega la scheda logica al PC tramite cavo USB.
2. Carica il programma corrispondente al servomotore (tabella 5.1).
3. Al termine del caricamento, scollega il cavo USB.
4. Importante: non alimentare mai la scheda con USB collegato e alimentazione esterna contemporaneamente.
5. Se il servomotore é di flessione (piegamento dita tramite tendini):
1. Avvita un bullone in uno dei fori della piastra circolare.
2. Ruota la piastra finché il foro con il bullone si trova in basso a destra (figura 5.9).
6. Se il servomotore é di rotazione del pollice:
1. Posiziona il pollice a circa meta del range (figura 5.8).
7. Collega il servomotore alla scheda logica (lascia scollegati tutti gli altri).
8. Alimenta la scheda logica con il connettore di alimentazione (non con il cavo USB!)
9. Il programma esegue automaticamente:
1. registrazione dell’ID del servomotore
2. registrazione della posizione centrale del range
3. 4 oscillazioni della piastra al termine della procedura (per confermare esito positivo)
10. Importante: Spegni la scheda logica scollegando l’alimentazione.
11. Importante: Scollega il servomotore dalla scheda logica.

TABELLA 5.1: Servomotore / Programma di registrazione (per la scheda logica)
Servomotore | Programma di registrazione
Rotazione Pollice | Thumb Rotation Registration Program
Flessione Pollice | Thumb Flexion Registration Program
Flessione Indice | Index Flexion Registration Program
Flessione Medio | Middle Flexion Registration Program
Flessione Anulare | Ring Flexion Registration Program
Nota: Il servomotore del mignolo non è presente perchè viene gestito dal motore dell'anulare.

Figure 5.9: Registrazione

servomotore di flessione | Figure 5.8: Registrazione servomotore rotazione pollice

## 5.2 Programmazione della scheda logica col programma operativo

Una volta registrati i servomotori, è necessario programmare la scheda con il programma operativo della mano robotica. Il programma è 'RebeliaRobot'.
1. SCOLLEGARE I SERVOMOTORI DALLA SCHEDA
2. Aprire Arduino IDE
3. Selezionare la board: ESP32-WROOM-DA Module
4. Aprire il programma RebeliaRobot.ino
5. Scollegare il connettore power dalla scheda logica
6. Collegare la scheda logica al PC con il cavo usb
7. Fare Upload del programma da Arduino IDE
8. Attendere il completamento dell'operazione
9. Scollegare il cavo usb dalla scheda logica
10. Collegare il connettore power alla scheda logica

5.2.1 Collegamento servomotori
I servomotori sono collegati alla scheda logica in daisy chain, vedi figure 5.10 e 5.11.
1. Collegare la scheda logica al servomotore 2
2. Collegare il servomotore 2 al servomotore 3
3. Collegare il servomotore 3 al servomotore 1
4. Collegare il servomotore 1 al servomotore 4, facendo prima entrare il cavo nella cavita’ S1 e facendolo uscire dalla cavita’ S2
5. Collegare il servomotore 4 al servomotore 5, facendo entrare il cavo nella cavita’ S3
A questo punto tutti i servomotori sono collegati alla scheda logica in daisy chain.

Figure 5.10: Vista anteriore. ID Servomotori, scheda logica PCB e cavita S1

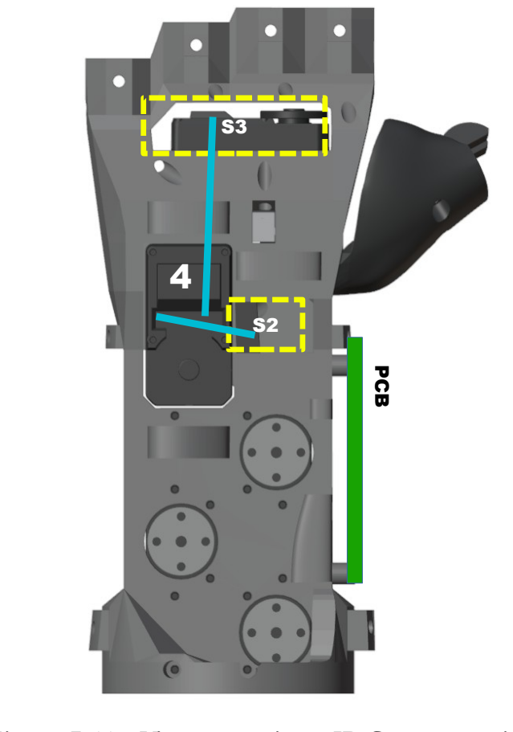
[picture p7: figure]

Figure 5.11: Vista posteriore. ID Servomotori, scheda logica PCB e cavita S2

## 5.3 Installazione scheda logica

1. Installare la scheda logica sullo scheletro come mostrato in figura 5.12, usanto 4 viti autofilettanti M2 lunghe 6 mm.

Figure 5.12: Scheda logica installata

## 5.4 Installazione tendini nelle dita

5.4.1 Installazione tendini nelle dita superiori

ATTENZIONE: I tendini
possono tagliare le dita!
OBBLIGATORIO: Usare la morsa per fermare lo scheletro e la pinza manuale di montaggio per tirare il tendine.

Installazione tendine dito indice (la stessa procedura vale anche per le dita medio, anulare e mignolo):
Nota: Al momento il KIT di assemblaggio viene fornito con i tendini gia installati sulle dita.

5.4.2 Installazione tendine nel pollice

ATTENZIONE: I tendini
possono tagliare le dita!
OBBLIGATORIO: Usare la morsa per fermare lo scheletro e la pinza manuale di montaggio per tirare il tendine.

Nota: Al momento il KIT di assemblaggio viene fornito con i tendini gia installati sulle dita.

## 5.5 Installazione dita Indice, Medio, Anulare e Mignolo

Nota: ogni dito va fissato, nel suo slot sullo scheletro, con un bullone M3 da 10mm.
1. Infilare il dito nel suo slot sullo scheletro (figura 5.13)
1. lasciare i tendini fuori, verranno inseriti nei fori dello scheletro successivamente in un’altra procedura
2. Posizionare il dado nella sua sede sulla parte anteriore dello scheletro (figura 5.14)
3. Fissare il dado con il tool di inserimento fornito (figura 5.16)
1. Nota: il tool serve anche a mantenere il dado fermo nella sua sede esagonale mentre si avvita il bullone
4. Inserire il bullone nel foro sulla parte posteriore dello scheletro e avvitare (figura 5.15)

Figure 5.14: Slot dita

### SLOT DITA

Figure 5.13: Sede dadi

### SEDE DADI

Figure 5.15: Inserimento bullone

Bullone

Figure 5.16: Tool
inserimento e
mantenimento dadi

## 5.6 Installazione dito Pollice

Nota: il pollice va fissato, nel suo slot sulla base pollice, con due bulloni M3 a testa svasata, uno lungo 16mm e uno lungo 20mm.
1. Infilare il dito nello slot (figura 5.17)
2. Inserire due bulloni da dietro (figura 5.17)
1. Bullone 1: M3 a testa svasata lungo 16 mm
2. Bullone 2: M3 a testa svasata lungo 20 mm
3. Fissare con due dadi M3 posti sul lato opposto (figura 5.18)

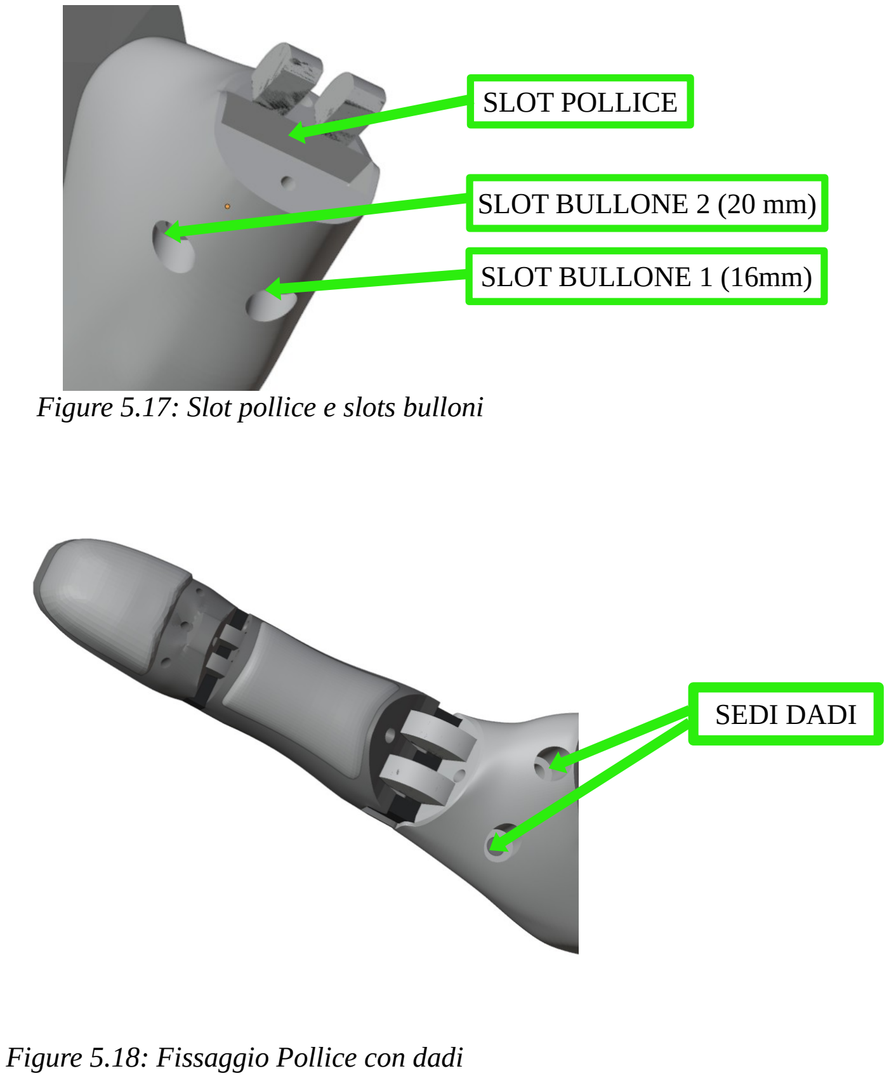
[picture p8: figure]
SLOT POLLICE; SLOT BULLONE 1 (16mm); SLOT BULLONE 2 (20 mm); Figure 5.18: Fissaggio Pollice con dadi; SEDI DADI

Figure 5.17: Slot pollice e slots bulloni

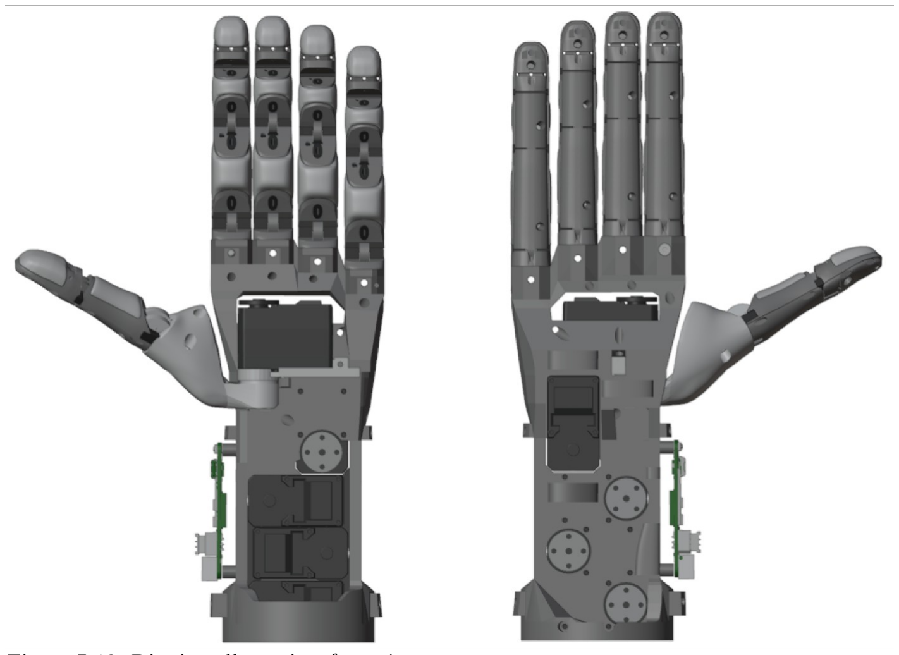
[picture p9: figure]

Figure 5.19: Dita installate, vista fronte/retro

## 5.7 Installazione tubi Bowden

5.7.1 Installazione tubo Bowden dito Indice

Per il solo dito INDICE:
1. Tendine di flessione:
1. Inserire il tubo in PTFE nel foro di uscita (sulla parte posteriore dello scheletro) del tendine di flessione (figura 5.20), farlo uscire dal foro di entrata sulla parte anteriore dello scheletro e inserirlo nello slot iniziale (figura 5.22)
2. Prendere la parte restante (sulla parte posteriore dello scheletro) e inserirla nello slot finale mostrato in figura 5.21.
3. Nota: se il tubo e' troppo lungo accorciarlo tagliandolo con un taglierino.
2. Tendine di estensione:
1. Inserire un capo del tubo in PTFE nello slot iniziale (sulla parte posteriore dello scheletro) del tendine di estensione (figura 5.24)
2. Inserire l'altro capo nello slot finale mostrato in figura 5.23: se il tubo e' troppo lungo accorciarlo tagliandolo con un taglierino.

Figure 5.20: Inserimento tubo nel foro di uscita del tendine (vista posteriore)

Figure 5.21: Inserimento tubo nello slot iniziale (vista anteriore)

Figure 5.22: Inserimento tubo nello slot finale (vista posteriore)

Figure 5.24: Inserimento tubo nello slot iniziale (vista posteriore)

Figure 5.23: Inserimento tubo nello slot finale (vista posteriore)

SLOT FINALE

5.7.2 Installazione tubo Bowden dito Medio

Per il solo dito MEDIO:
1. Tendine di flessione:
1. Inserire il tubo in PTFE nel foro di uscita (sulla parte posteriore dello scheletro) del tendine di flessione (figura 5.26), farlo uscire dal foro di entrata sulla parte anteriore dello scheletro e inserirlo nello slot iniziale (figura 5.27)
2. Prendere la parte restante (sulla parte posteriore dello scheletro) e infilarla prima attraverso i 2 tunnel di passaggio e poi nello slot finale (figura 5.25).
3. Nota: se il tubo e' troppo lungo accorciarlo tagliandolo con un taglierino.
2. Tendine di estensione:
1. Inserire un capo del tubo in PTFE nello slot iniziale (sulla parte posteriore dello scheletro) del tendine di estensione (figura 5.28)
Inserire l'altro capo nello slot finale mostrato in figura 5.29
2. Nota: se il tubo e' troppo lungo accorciarlo tagliandolo con un taglierino.

Figure 5.26 Inserimento tubo nei due tunnel di passaggio e infine nello slot finale (vista posteriore); TUNNEL; SLOT FINALE

Figure 5.27: Inserimento tubo nel foro di uscita del tendine (vista posteriore)

Figure 5.25: Inserimento nello slot circolare (vista anteriore)

SLOT NIZIALE

Figure 5.29 Inserimento tubo nello slot iniziale (vista posteriore)

Figure 5.28 Inserimento tubo nello slot finale (vista posteriore)

SLOT FINALE

5.7.3 Installazione tubo Bowden dito Anulare

Per il solo dito ANULARE
1. Tendine di flessione:
1. Inserire il tubo in PTFE nel foro di uscita (sulla parte posteriore dello scheletro) del tendine di flessione (figura 5.31), farlo uscire dal foro di entrata sulla parte anteriore dello scheletro e inserirlo nello slot iniziale (figura 5.32)
2. Prendere la parte restante (sulla parte posteriore dello scheletro) e infilarla prima nel tunnel di passaggio e poi nello slot finale finale (figura 5.30).
3. Nota: se il tubo e' troppo lungo accorciarlo tagliandolo con un taglierino.
2. Tendine di estensione:
1. Inserire un capo del tubo in PTFE nello slot iniziale (sulla parte posteriore dello scheletro) del tendine di estensione (figura 5.34)
2. Inserire l'altro capo nel tunnel di passaggio e poi nello slot finale (figura 5.33).
3. Nota: se il tubo e' troppo lungo accorciarlo tagliandolo con un taglierino.

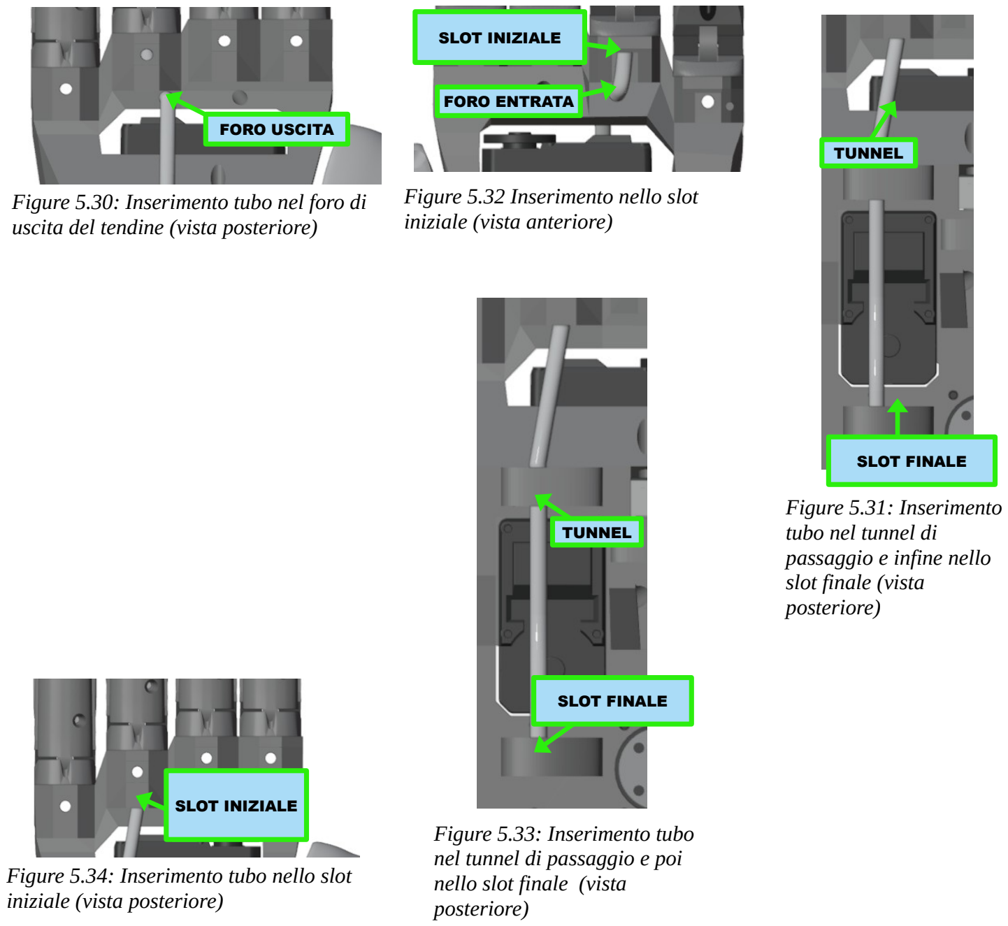
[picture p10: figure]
uscita del tendine (vista posteriore); FORO USCITA; Figure 5.32 Inserimento nello slot iniziale (vista anteriore); FORO ENTRATA; SLOT INIZIALE; Figure 5.31: Inserimento tubo nel tunnel di passaggio e infine nello slot finale (vista posteriore); SLOT FINALE; TUNNEL; iniziale (vista posteriore); Figure 5.33: Inserimento tubo nel tunnel di passaggio e poi nello slot finale (vista posteriore)

Figure 5.30: Inserimento tubo nel foro di

Figure 5.34: Inserimento tubo nello slot

5.7.4 Installazione tubo Bowden dito Mignolo

Per il solo dito MIGNOLO
1. Tendine di flessione:
1. Inserire il tubo in PTFE nel foro di uscita (sulla parte posteriore dello scheletro) del tendine di flessione (figura 5.37), farlo passare nel tunnel di passaggio e farlo uscire dal foro di entrata sulla parte anteriore dello scheletro e inserirlo nello slot iniziale (figura 5.36).
2. Prendere la parte restante (sulla parte posteriore dello scheletro) e infilarla prima nel tunnel di passaggio e poi nello slot finale (figura 5.35).
3. Nota: se il tubo e' troppo lungo accorciarlo tagliandolo con un taglierino.
2. Tendine di estensione:
1. Inserire un capo del tubo in PTFE nello slot iniziale (sulla parte posteriore dello scheletro) del tendine di estensione (figura 5.39).
2. Inserire l'altro capo nel tunnel di passaggio e poi nello slot finale (figura 5.38).
3. Nota: se il tubo e' troppo lungo accorciarlo tagliandolo con un taglierino.

Figure 5.35 Inserimento tubo nel tunnel di passaggio e infine nello slot finale (vista posteriore); SLOT FINALE; TUNNEL

Figure 5.37 Inserimento tubo nel foro di uscita del tendine (vista posteriore)

Figure 5.36 Inserimento nello slot iniziale (vista anteriore)

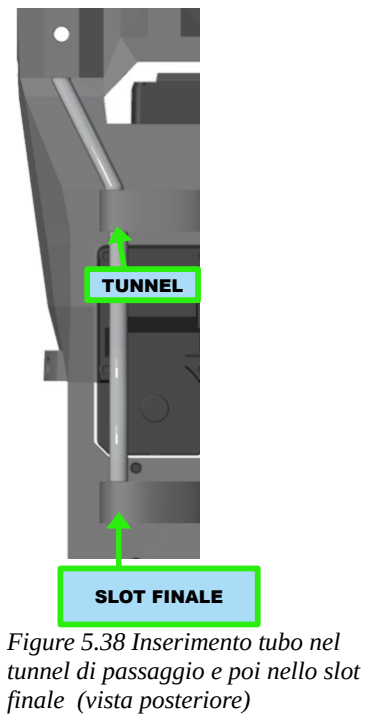
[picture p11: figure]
Figure 5.38 Inserimento tubo nel tunnel di passaggio e poi nello slot finale (vista posteriore); SLOT FINALE; TUNNEL

Figure 5.39 Inserimento tubo nello slot iniziale (vista posteriore)

5.7.5 Controllo installazione tubi Bowden
Prima di procedere assicurarsi che i tubi bowden siano tutti installati correttamente come in figura.

Figure 5.41: Vista anteriore con tubi bowden installati

Figure 5.40: Vista posteriore con tubi bowden installati

## 5.8 Inserimento tendini nei tubi Bowden (estremità di flessione)

Procedura da applicare solo ai tendini delle dita: indice, medio, anulare e mignolo.
Per questa operazione serve un ago in nylon lungo almeno 20 cm (filo steso 40 cm).
Per ogni dito:
1. Sulla parte anteriore dello scheletro, inserire i due capi dell'ago in nylon nel foro di entrata davanti allo slot del dito (figura 5.43) e spingerli nel tubo in PTFE sottostante, facendoli uscire dal foro di uscita sulla parte posteriore dello scheletro (figura 5.42)
2. Inserire l'estremità di flessione del tendine nell'asola dell'ago in nylon rimasta fuori dal foro di entrata (figura 5.43) e tirare dall'altro capo del tubo bowden i capi dell'ago in nylon, finché tutto il tendine non esce fuori dal foro di uscita (figura 5.44).

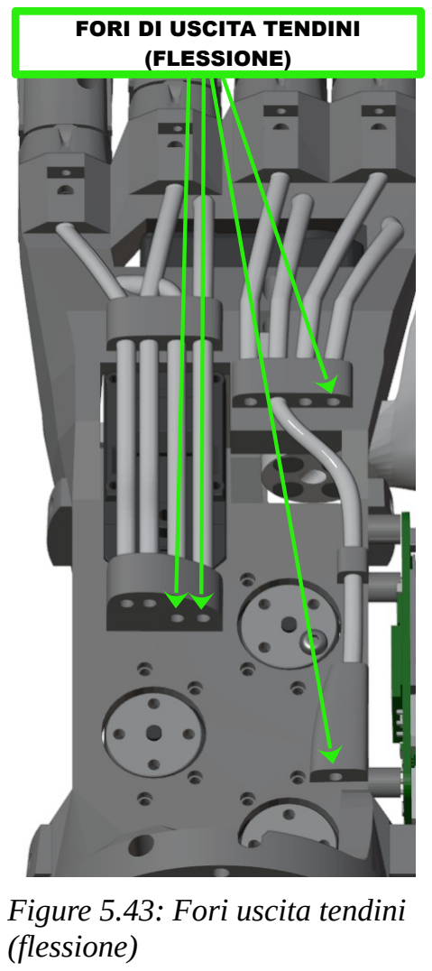
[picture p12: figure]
Figure 5.43: Fori uscita tendini (flessione); FORI DI USCITA TENDINI (FLESSIONE)

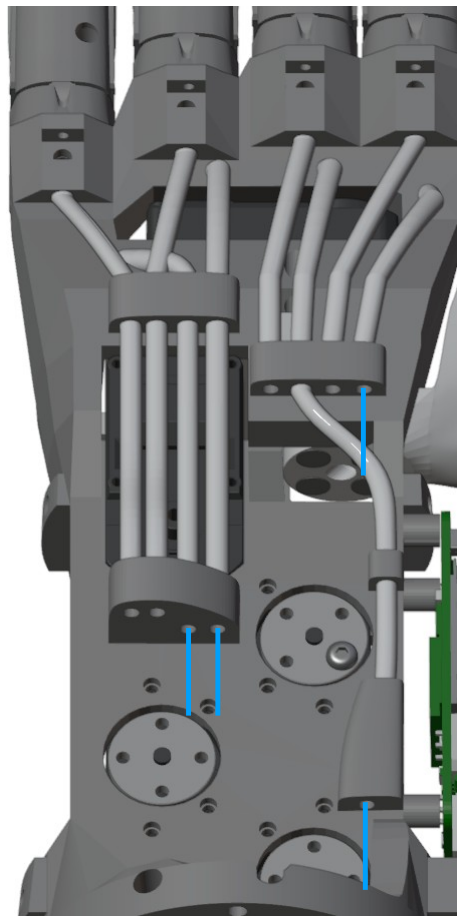
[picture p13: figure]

Figure 5.44: Estermita di flessione dei tendini uscenti dai tubi bowden

## 5.9 Inserimento tendini nei tubi Bowden (estremità di estensione)

Procedura da applicare solo ai tendini delle dita: indice, medio, anulare e mignolo.
Per questa operazione serve un ago in nylon lungo almeno 20 cm (filo steso 40 cm).
Per ogni dito:
3. Sulla parte posteriore dello scheletro: inserire i due capi dell'ago in nylon nel foro finale del dito e poi nel sottostante foro di entrata del tubo bowden (figura 5.46).
4. Spingere i fili di nylon fino a farli uscire dal foro di uscita (figura 5.45).
5. Inserire l'estremità di estensione del tendine nell'asola dell'ago in nylon rimasta fuori dal foro finale del dito (figura 5.46) e tirare dall'altro capo del tubo bowden i capi dell'ago in nylon, finché tutto il tendine non esce fuori dal foro di uscita (figura 5.47)

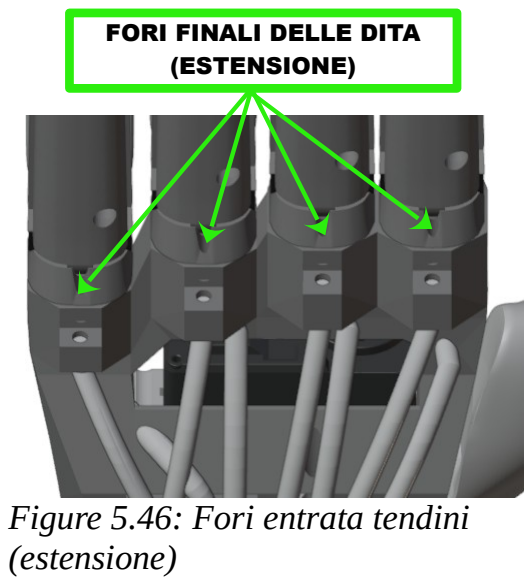
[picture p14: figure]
Figure 5.46: Fori entrata tendini (estensione); FORI FINALI DELLE DITA (ESTENSIONE)

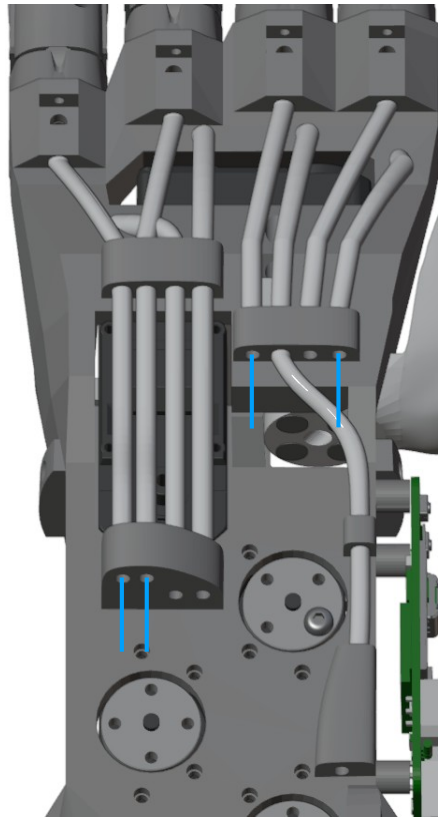
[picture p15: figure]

Figure 5.47: Estermita di estensione dei tendini uscenti dai tubi bowden

## 5.10 Installazione tendini su avvolgitori

5.10.1 Informazioni sulla Sicurezza
!! NON TIRARE IL TENDINE A MANI NUDE !! OBBLIGATORIO
- Usare una morsa per tenere ferma la parte su cui operare
- | Usare una pinza manuale di montaggio per | tirare il tendine
POSSIBILI DANNI:
- Gravi tagli alle dita
- Dissanguamento

OBBLIGO DI USARE LA MORSA

OBBLIGO DI USARE LA PINZA MANUALE DI MONTAGGIO

PERICOLO DI TAGLIO DITA

5.10.2 Tecnica dell'ago in nylon
I tendini sono sottili e difficili da infilare, per questo bisogna usare un ago speciale.
Questo ago speciale è in realtà un filo di nylon usato come se fosse un ago.
È stato scelto questo metodo in seguito a molteplici tentativi, usando vari strumenti diversi, in quanto si è rivelato essere il più rapido ed affidabile e sicuro.
Di seguito è mostrata la procedura per infilare il tendine in un foro usando un filo di nylon (i 10 cm, 0.35 mm diametro) come ago:

ATTENZIONE: I tendini possono tagliare le dita! OBBLIGATORIO: Usare la morsa per fermare la avvolgitore e la pinza manuale di montaggio per tirare il tendine.

NOTA: In seguito ci riferiremo a questa sequenza di operazioni semplicemente dicendo: "infilare il tendine". E' implicitamente assunto che va fatto usando l'ago in nylon.

Figure 5.48: Infilare i capi del filo di nylon, uno alla volta, nel foro

Figure 5.49: Infilare il tendine nel cappio di nylon

Figure 5.51: tirare con la pinza manuale di montaggio la parte più corta del tendine dall'altro lato del foro

Figure 5.50: Tirare con la pinza manuale di montaggio i due capi del cappio di nylon dall'altro lato del foro

5.10.3 Installazione tendini su avvolgitori (indice, medio, anulare e mignolo)

ATTENZIONE: I tendini
possono tagliare le dita!
OBBLIGATORIO: Usare la morsa per fermare lo scheletro e la pinza manuale di montaggio per tirare il tendine.

5.10.3.1 Preparazione assemblato avvolgitori
Ogni servo necessita di un avvolgitore di flessione e uno di estensione, che sono montati uno sopra l'altro. Vedi figura.
Per ogni avvolgitore di flessione (disegnato in giallo in figura 5.52):
1. Posizionare sopra di esso l'avvolgitore di estensione (disegnato in blu in figura 5.52)
1. Accertarsi che l’avvolgitore di flessione (in giallo in figura 5.52) abbia il diametro piu piccolo in basso.
2. Fissare l'avvolgitore di estensione con 4 bulloni M3 da 10 mm con testa a bottone (figura 5.53): le viti terranno momentaneamente l'assemblato insieme per semplice incastro, senza avvitamento (é importante che rimangano uniti fino alla fine della fase successiva 'Installazione tendini sugli avvolgitori').

Figure 5.53:
Assemblato avvolgitori

Figure 5.52: I bulloni
mantengono unito
l'assemblato

5.10.3.2 Installazione tendini sugli avvolgitori
Assicurarsi che gli assemblati avvolgitori siano ognuno correttamente assemblato (le viti tengono momentaneamente uniti l'avvolgitore di estensione a quello di flessione per semplice incastro, senza avvitamento)
Preparazione:
1. Assicurarsi che i servomotori siano tutti collegati, e che gli avvolgitori non siano installati.
2. Alimentare la scheda logica usando il connettore power (assicurarsi che il cavo USB sia scollegato) come mostrato in figura 5.54.
3. Collegarsi (FORNIRE TOOL PER BT SERIAL) via Bluetooth al dispositivo (nome device: YEAH-HAND-X-YYYYYY, dove X è 'L' o 'R' a seconda del modello, e YYYYYY è il numero seriale)
4. inviare via Bluetooth il comando seriale di selezione 'INSTALL'.
5. aspettare che i servomotori completino il loro movimento e procedere con i seguenti paragrafi:
1. Installazione tendini negli avvolgitori (indice, medio, anulare e mignolo)
2. Installazione tendini negi avvolgitori (pollice)

Figure 5.54:
Connettore power
inserito

Installazione tendini negli avvolgitori (indice, medio, anulare e mignolo):
1. Per ogni servomotore:
1. Individuare il relativo dito (o le dita nel caso di anulare e mignolo) e il relativo assemblato avvolgitori (avvolgitore di flessione e avvolgitore di estensione sono attualmente tenuti insieme dai bulloni infilati, ma non ancora avvitati a nulla)
2. Prendere l'estremita di flessione del tendine (2 estremità nel caso di anulare e mignolo)
3. Infilare l'estremità (o le estremità) nel foro in basso a destra dell'avvolgitore di flessione e farlo uscire dal foro corrispontente dell'avvolgitore di estensione (figura 5.56), assicurarsi che la quantità di tendine uscito dal foro sia abbastanza lunga da evitare che si sfili nuovamente.
4. Assicurarsi che l'assemblato avvolgitori non si smonti durante le operazioni.
5. Prendere l'estremità di estensione del tendine (2 estremità nel caso di anulare e mignolo)
6. Infilare l'estermità (o le estremità) nel foro in alto dell'avvolgitore di estensione e farlo uscire dal foro in basso dello stesso avvolgitore (figura 5.55), assicurarsi che la quantità di tendine uscito dal foro sia abbastanza lunga da evitare che si sfili nuovamente.
7. Posizionare l'assemblato avvolgitori sul relativo servomotore, con la freccia in alto (figura 5.28)
8. Avvitare l'assemblato avvolgitori alla flangia del relativo servomotore con i bulloni M3
9. Completamento estremita di estensione del tendine:
1. Far sì che il tendine compia un giro orario intorno all’avvolgitore di estensione prima che entri nel foro superiore (figura 5.60)
2. Tirare il tendine dal foro inferiore (finche il dito non sta dritto) e farlo ruotare attorno al bullone sinistro con una rotazione oraria attorno a esso (figura 5.59).
3. Mentre si tiene tirato il tendine con una pinza manuale di montaggio, stringere bene il bullone con la chiave per bloccare il tendine (figura 5.58)
10. Completamento estremita di flessione del tendine:
1. Tirare il tendine finchè non è teso, senza spostare la posizione del dito controllato, e farlo ruotare attorno al bullone destro con una rotazione oraria attorno a esso (figura 5.61).
2. Mentre si tiene tirato il tendine con una pinza manuale di montaggio, stringere bene il bullone per bloccare il tendine (figura 5.62).

Figure 5.56: Inserimento estremita di flessione; FORO ENTRATA; FORO USCITA

Figure 5.55:
Inserimento estremita
di estensione

Figure 5.57: Assemblati
Avvolgitori montati con
freccia in alto

Figure 5.61: Estremita di
flessione: Rotazione attorno al bullone

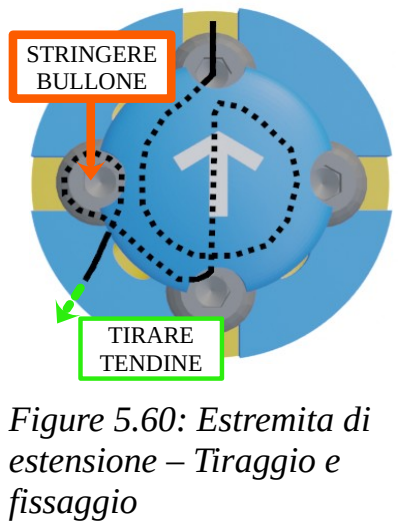
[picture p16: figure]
Figure 5.60: Estremita di estensione – Tiraggio e fissaggio; TIRARE TENDINE; STRINGERE BULLONE

Figure 5.58: Operazione di pre-avvolgimento estremita di estensione del tendine

Installazione tendini negli avvolgitori (pollice)
Nota: il pollice usa un solo avvolgitore sia per estensione che per flessione.
1. Solo per il servomotore del pollice
1. Prendere l'estremita di flessione del tendine
2. Infilare l'estremità nel foro in alto a destra dell'avvolgitore e farlo uscire dal foro corrispontente di uscita (figura 5.64), assicurarsi che la quantità di tendine uscito dal foro sia abbastanza lunga da evitare che si sfili nuovamente.
3. Prendere l'estremità di estensione del tendine
4. Infilare l'estermità nel foro in basso a sinistra dell'avvolgitore e farlo uscire dal foro corrispondente di uscita dello stesso avvolgitore (figura 5.65), assicurarsi che la quantità di tendine uscito dal foro sia abbastanza lunga da evitare che si sfili nuovamente.
5. Posizionare l'avvolgitore sul relativo servomotore e fissarlo con 4 bulloni M3 (figura 5.66)
6. Tirare l’estremitá di estensione del tendine dal foro inferiore (finche il dito non sta dritto) e fissarlo al bullone in basso con una rotazione oraria attorno a esso (figura 5.67). Mentre si tiene tirato il tendine con una pinza manuale di montaggio, stringere bene il bullone per bloccare il tendine (figura 5.38). La figura 5.63 mostra l'operazione completata.
7. Tirare l'estremita di flessione del tendine di flessione senza spostare la posizione del dito e fissarlo al bullone in alto con una rotazione oraria attorno a esso (figura 5.68). Mentre si tiene tirato il tendine con una pinza manuale di montaggio, stringere bene il bullone per bloccare il tendine (figura 5.68). La figura 5.69 mostra l'operazione completata.

Figure 5.63: Avvolgitore
Pollice : Inserimento
estremita di flessione

Figure 5.64: Avvolgitore Pollice : Inserimento estremita di estensione; FORO ENTRATA

FORO ENTRATA | FORO USCITA

Figure 5.65: Posizionare
avvolgitore su servomototre

Figure 5.66: Rotazione
attorno a bullone e fissaggio

Figure 5.67: Tendine
fissato sotto al bullone

Figure 5.69: Rotazione
attorno a bullone

Figure 5.68: Tendine fissato sotto al bullone

## 5.11 Installazione palmo

Posizionare il palmo e fissarlo con 4 viti M2 lunghe 6 – 8mm (vedi figura )

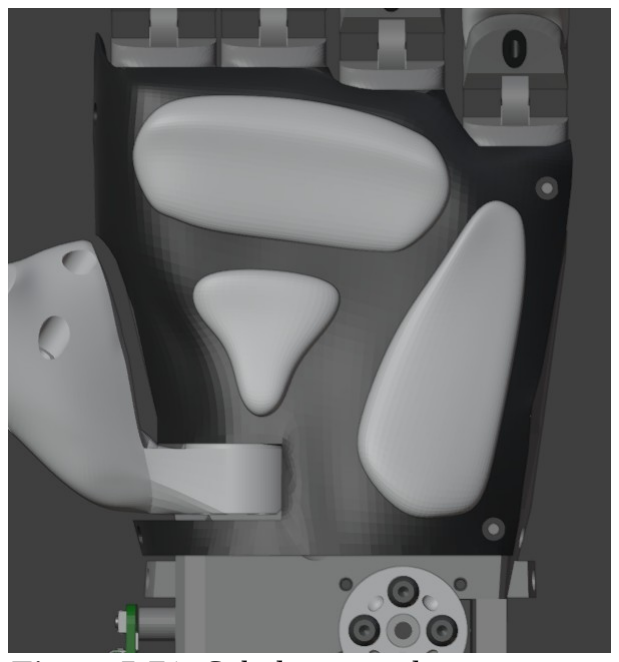
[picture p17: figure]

Figure 5.70: Scheletro - zona del palmo | Figure 5.71: Scheletro - palmo installato

## 5.12 Installazione covers

5.12.1 Installazione cover superiore
Posizionare i pin del lato pollice nei fori dello scheletro, incastrarli, poi ruotando la cover procedere all'incastro dei pin sull'altro lato (vedi figure 5.73 e 5.72).

Figure 5.73: Scheletro - Area della cover superiore

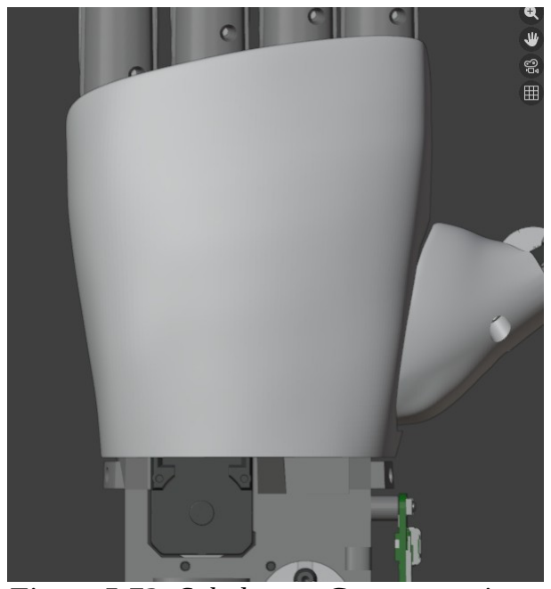
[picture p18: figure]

Figure 5.72: Scheletro - Cover superiore montata

5.12.2 Installazione covers inferiori
1. Assicurarsi che sullo scheletro già stata montata la scheda logica
2. Assicurarsi che la scheda logica sia collegata al servomotore alla base dello scheletro con il cavo di controllo
3. Posizionare i pin su un lato della cover posteriore sui fori di incastro del lato corrispodente dello scheletro, incastrarli, poi ruotando la cover procedere all incastro dei pin sull'altro lato. Vedi figure 5.74 e 5.75.
4. Posizionare i pin su un lato della cover anteriore sui fori di incastro del lato corrispodente dello scheletro, incastrarli, poi ruotando la cover procedere all incastro dei pin sull'altro lato. Vedo figure 5.76 e 5.77.

Figure 5.74: Scheletro - Area cover inferiore posteriore

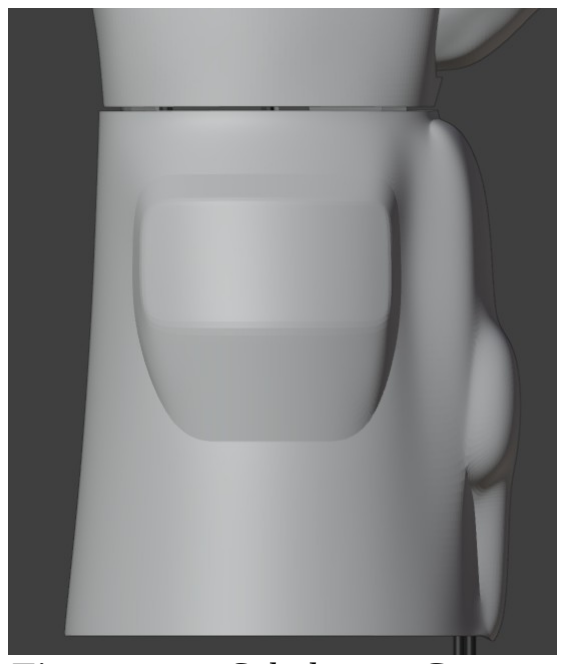
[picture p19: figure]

Figure 5.75: Scheletro - Cover inferiore posteriore installata

Figure 5.77: Scheletro - Cover inferiore anteriore montata

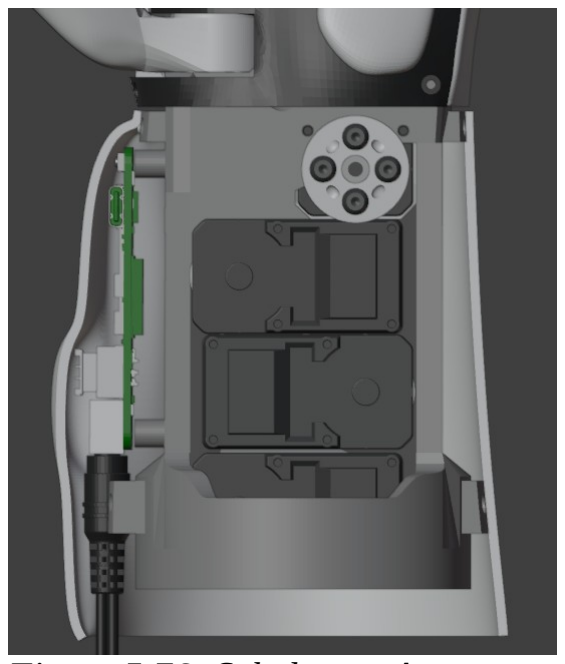
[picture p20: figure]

Figure 5.76: Scheletro - Area cover inferiore anteriore

5.12.3 Installazione covers dita
Per ogni dito superiore (indice, medio, anulare, mignolo)
1. posizionare la cover distal sulla falange distale e premere per incastrarla
2. posizionare la cover medial sulla falange medial e premere per incastrarla
3. posizionare la cover proximal sulla falange proximal e premere per incastrarla

Per il pollice:
1. posizionare la cover distal sulla falange distale e premere per incastrarla
2. posizionare la cover proximal sulla falange proximal e premere per incastrarla

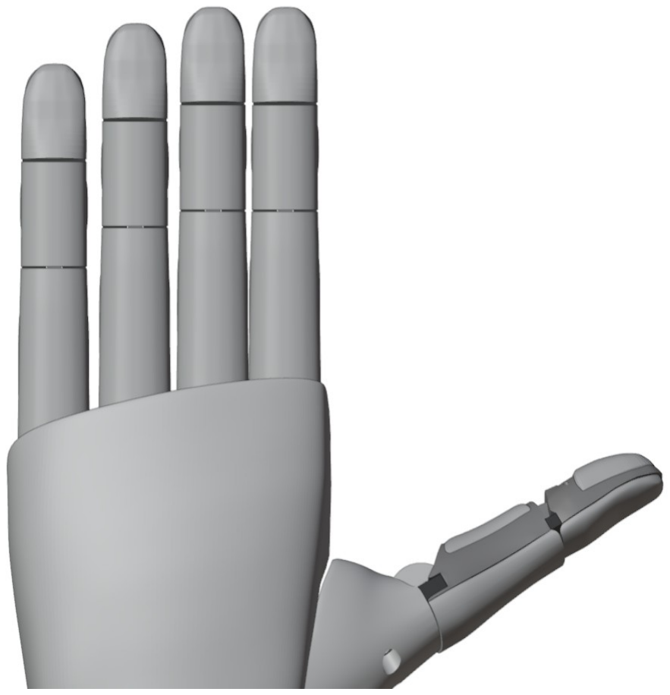
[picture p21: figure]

Figure 5.78: Covers installate sulle dita

## 6 Installazione della mano robotica su Robot Manipolatore

1. Posizionare la flangia sul robot wrist, allineare con il perno di allineamento.
2. Avvitare con 4 bulloni M6 a testa svasata lunghi 3 cm. TBD
3. Posizionare la mano robotica sulla flangia secondo l’orientamento desiderato.
4. Fissare con 4 bulloni a testa svasata M3 lunghi 3 cm. TBD
5. Collegare il connettore del cavo di alimentazione della mano robotica al connettore del robot
| wrist.

La scheda logica fornita (WaveShare ESP32 Servo Driver Board) richiede 12V DC.
Se e' necessario alimentare la mano robotica a 24V DC, bisogna installare la scheda di conversione tensione, che porta la tensione da 24V a 12V. In quel caso il fusibile da usare é di 2 A.

USARE SOLO ALIMENTATORI CON QUESTE CARATTERISTICHE DI USCITA: TENSIONE: 12V DC
2A < CORRENTE < 5A

In base all'alimentazione disponibile, installare il fusibile appropriato (vedi tabella).

Alimentazione DC | Fusibile da installare
12V 2A | 2A
12V 4A | 4A
12V 5A | 5A
24V 2A + Scheda Conversione a 12V 4A | 4A
24V 1A + Scheda Conversione a 12V 2A | 2A

TODO METTERE FIGURE SCHEDA CONVERSIONE 24/12

## 7 Impostazioni originali del fabbricante dell’attrezzatura

Le impostazioni predefinite della mano robotica sono queste:
| • Modalità di controllo ◦ Grasp Control ▪ MONKEY GRASP • Posizione dita: ◦ factor: 0% (massima apertura) • Nome device Bluetooth: ◦ YeahHand_XXX, dove XXX é un codice univoco.

## 8 Funzionamento

LEGGERE IL MANUALE PRIMA DI USARE LA MANO ROBOTICA

LEGGERE LE INFORMAZIONI SUL FUNZIONAMENTO TIPICO

## 8.1 Avviamento

Per avviare la mano robotica, attivare l’alimentazione dai comandi del braccio robotico su cui è installato, in modo che il connettore del robot wrist eroghi 12V e almeno 162 W di potenza.
La mano robotica inizia la fase di auto-calibrazione tendini, una volta completata la mano robotica sarà in posizione di massima apertura dita, in modalita grasping mode: monkey grasp. Connettersi alla mano robotica dal sistema di controllo del robot, tramite connessione seriale a caratteri BlueTooth (device name: YEAH-HAND-L_XXXXX oppure YEAH-HAND-R_XXXXX, dove XXXXX è il numero seriale della mano robotica.
I comandi seriali sono nel formato CMD X Y ...\r\n, dove CMD è la stringa di comando e X Y ... sono parametri aggiuntivi, mentre \r\n é la sequenza finale di invio (ritorno a capo e nuova linea)

## Configurazione

Al momento è possibile configurare i seguenti parametri:

Parametro | Command | Variables
PINCH Offset | SETPINCH X\r\n | X: [-40, 40] Pinch Offset
Load Limit | LIM X Y\r\n | X: [1, 5] Motor ID Y: [0, 600] Load Limit Value

## 8.2 Selezione modalità di controllo

Modalita di controllo | Comando completo
Monkey grasp | MONKEY\r\n
Power grasp | POWER\r\n
Pinch grasp ¹ | PINCH\r\n
Relax | RELAX\r\n
RAW | RAW\r\n

1

Il gesto PINCH richiede la configurazione del pinch offset tramite il comando SETPINCH, vedi paragrafo relativo.

## 8.3 Movimento dita

8.3.1 Modalita Grasp Control
Se è stata selezionata una modalita tra MONKEY, POWER, POWERSMALL, PINCH, la mano robotica puo essere comandato in questo modo:
- Comando: X\r\n
- Significato: X esprime il valore integer [0, 100] esprimente la percentuale di chiusura dita (ogni tipo di grasp selezionato applica la chiusura a tutte le dita in modo differente dalgli altri grasp)

Esempi:

ESEMPIO | COMANDO COMPLETO
Apertura massima | 0\r\n
Chiusura massima | 100\r\n
Chiusura 50% | 50\r\n
Chiusura 75% | 75\r\n

8.3.2 Modalità ROS
Se è stata selezionata una modalita ‘ROS’, la mano robotica puo essere comandato in questo modo:
- Comando: ROS V W X Y Z\r\n
- Significato:
- ROS : tag iniziale del pacchetto dati
- V esprime un integer col valore chiusura [0, 100] per index flexion
- W esprime un integer col valore chiusura [0, 100] per middle flexion
- X esprime un integer col valore chiusura [0, 100] per ring flexion
- Y esprime un integer col valore chiusura [0, 100] per thumb flexion
- Z esprime un integer col valore chiusura [0, 100] per thumb rotation

Esempi:

ESEMPIO | COMANDO COMPLETO
Flessione Indice: 30% Flessione Medio: 50% Flessione Anulare e mignolo: 10% Flessione Pollice: 70% Rotazione Pollice: 65% | ROS 30 50 10 70 65\r\n
Flessione Indice: 10% Flessione Medio: 20% Flessione Anulare e mignolo: 30% Flessione Pollice: 40% Rotazione Pollice: 50% | ROS 10 20 30 40 50\r\n
Flessioni : massima apertura Rotazione pollice: massima apertura (mano aperta) | ROS 0 0 0 0 0\r\n
Flessioni : massima chiusura Rotazione pollice: massima chiusura (pollice in opposizione) | ROS 100 100 100 100 100\r\n

## 9 Cambio di prodotto o di capacità

Prima di sostituire un oggetto preso dalla mano robotica, assicurarsi che le sue caratteristiche rientrino nei limiti esposti nel capitolo Caratteristiche tecniche della macchina alla sezione "Proprietà dell'oggetto".

## 10 Ispezioni, prove e manutenzione

## 10.1 Ciclo di vita prevista dei componenti

Nota: Un ciclo è una chiusura completa del dito dalla posizione 0% (completamente aperto) alla posizione 100% (completamente chiuso, pari a 300° di rotazione del servomotore) e successiva riapertura alla posizione 0%.

COMPONENTE | DURATA IN CICLI²
Scheletro | 200000
TRS Platform | 200000
Base pollice | 20000
Dita | 20000
Avvolgitori | 20000
Covers | 200000
Tendini e tubi bowden | 200000
Servomotori ³ | 20000
Scheda logica | 200000

## 10.2 Natura - frequenza e criteri di ispezione

COMPONENTE | INTERVALLO DI ISPEZIONE IN CICLI
Scheletro | 50000
TRS Platform | 50000
Base pollice | 5000
Dita | 5000
Avvolgitori | 5000
Covers | 50000
Tendini e tubi bowden | 50000
Servomotori | 5000
Scheda logica | 50000
2 | Valori trovati sperimentalmente con uso prolungato del prodotto (periodo 2024-2025-2026).
3 | Calcolato in base ai dati del fabbricante originale WaveShare. Il servomotore ST3215-HS ha una diurata di vita di
| 100000 cicli dove un ciclo consiste nel ruotare la flangia da 0° a 60° e poi di nuovo a 0

## 10.3 Specifiche dei ricambi

Tutti i ricambi sono specificati nella seguente tabella:

DESCRIZIONE | QUANTITA IN UN PRODOTTO | FABBRICANTE | MODELLO
scheletro | 1 | VITTORIO-LUMARE | H-SKELETON-X
indice con pads in silicone | 1 | VITTORIO-LUMARE | H-FING-IF-X
medio con pads in silicone | 1 | VITTORIO-LUMARE | H-FING-MF-X
anulare con pads in silicone | 1 | VITTORIO-LUMARE | H-FING-RF-X
mignolo con pads in silicone | 1 | VITTORIO-LUMARE | H-FING-LF-X
pollice con pads in silicone | 1 | VITTORIO-LUMARE | H-FING-TF-X
palmo con pads in silicone | 1 | VITTORIO-LUMARE | H-PALM-X
base pollice | 1 | VITTORIO-LUMARE | H-FING-TB-X
tubi bowden | 1 | VITTORIO-LUMARE | H-PTFE-TUBING-X
avvolgitore tendini | 4 | VITTORIO-LUMARE | H-SPOOL-X
cover anteriore | 1 | VITTORIO-LUMARE | R-COV-F-X
cover posteriore | 1 | VITTORIO-LUMARE | R-COV-B-X
gruppo covers indice | 1 | VITTORIO-LUMARE | H-FING-COV-IF-X
gruppo covers medio | 1 | VITTORIO-LUMARE | H-FING-COV-MF-X
gruppo covers anulare | 1 | VITTORIO-LUMARE | H-FING-COV-RF-X
gruppo covers mignolo | 1 | VITTORIO-LUMARE | H-FING-COV-LF-X
gruppo covers pollice | 1 | VITTORIO-LUMARE | H-FING-COV-TF-X
flangia per UR3 | 1 | VITTORIO-LUMARE | R-FLANGE-UR3-X
servomotori e cavi | 5 | WAVESHARE | ST3215-HS
scheda logica | 1 | WAVESHARE | Servo Driver with ESP32
tendini in polietilene (matassa) | 1 | HERCULES | 90.7 kg, 0.75mm, 8 strands
Bulloni M3, testa svasata, lunghi 20 mm | TBD | N.A. | N.A.
Bulloni M3, testa svasata, lunghi 16 mm | TBD | N.A. | N.A.
Bulloni M3, testa svasata, lunghi 12 mm | TBD | N.A. | N.A.
Bulloni M3, testa bottone, lunghi 10 mm | TBD | N.A. | N.A.
Bulloni M6, testa esagonale, lunghi 35 mm | TBD | N.A. | N.A.
Bulloni M3, testa svasata, lunghi 20 mm | TBD | N.A. | N.A.
Bulloni M2, testa cilindrica esagono incassato, lunghi 5 mm | TBD | N.A. | N.A.

Viti autofilettanti M2 lunghe 6mm | TBD | N.A. | N.A.

## 10.4 Attrezzature

10.4.1 Attrezzature per assemblaggio e manutenzione Questi sono gli strumenti e attrezzature richieste per l'assemblaggio

DESCRIZIONE | QUANTITA | FABBRICANTE | MODELLO
Cacciavite a Phillips #1 lungo per elettronica 6.69" | 1 | WIHA | 261110
Pinze di precisione 4.72" | 1 | ADAFRUIT INDUSTRIES LLC | 422
Cacciavite esagonale 2mm 5.71" | 1 | WIHA | 26320
Cacciavite esagonale 1.5mm 7.05" | 1 | WIHA | 36715
Pinza manuale di montaggio piccola | 1 | OLIMEX LTD | CHN-PLI-LC

## 10.5 Procedure di sezionamento delle energie

Per scollegare la fonte di energia elettrica che alimenta la mano robotica è sufficiente staccare la spina di alimentazione dal connettore laterale (figura 10.1).

Figure 10.1: Connettore con spina di alimentazione inserita

SPINA DI
ALIMENTAZIONE

## 10.6 Manutenzione Straordinaria

Queste operazioni vanno solo nel caso in cui un componente richieda sostituzione. 10.6.1 Sostituzione dita
Eseguire in sequenza:
1. Disinstallazione tendini
2. Disinstallazione dita
3. Installazione dita
4. Installazione tendini
5. Registrazione tendini

10.6.2 Disinstallazione dita

USARE LA MORSA

1. Svitare tutti i bulloni di fissaggio dita
2. Rimuovere tutte le dita dai loro slot

10.6.3 Installazione dita

USARE LA MORSA

Vedi capitolo 5.5.Installazione dita Indice, Medio, Anulare e Mignolo Vedi capitolo 5.1.5.Installazione dito pollice

10.6.4 Disinstallazione tendini

1. Tagliare tutti i tendini con le forbici
2. Svitare i bulloni di fissaggio tendini dal tutte gli avvolgitori usando la chiave esagonale fornita da 2.5mm
3. Rimuovere tutti i tendini usando la pinza manuale di montaggio fornita

10.6.5 Installazione tendini

Vedi capitolo 5.4.Installazione tendini nelle dita|outline

10.6.6 Sostituzione motori Eseguire in sequenza:
1. Disinstallazione motori
2. Installazione motori

10.6.7 Disinstallazione Motori
1. Rimuovere ogni servomotore svitando le 4 viti di fissaggio, rispettando questa sequenza:
1. servomotore di flessione dita anulare-mignolo
2. servomotore di flessione dito indice
3. servomotore di flessione dito medio
4. servomotore di flessione dito pollice
5. servomotore di rotazione dito pollice

10.6.8 Installazione Motori
Vedi capitolo 5.1.Installazione e registrazione servomotori

10.6.9 Sostituzione cover
Eseguire in sequenza:
1. Disinstallazione cover
2. Installazione cover

10.6.10 Disinstallazione cover
1. Smontare la cover anteriore a incastro (lato palmo)
2. Smontare la cover posteriore a incastro (lato dorso)

10.6.11 Installazione cover
Vedi capitolo Installazione covers

10.6.12 Sostituzione scheletro
Per sostituire lo scheletro è necessario smontare tutti i componenti e rimontare la mano robotica dall'inizio.
Eseguire in sequenza:
1. Disinstallazione Cover
2. Disinstallazione Scheda
3. Disinstallazione Tendini
4. Disinstallazione Tubi Bowden
5. Disinstallazione Avvolgitori
6. Disinstallazione Dita
7. Disinstallazione Servomotori inclusa TRS Platform
8. SOSTITUZIONE SCHELETRO
9. Installazione Servomotori inclusa TRS Platform
10. Installazione Dita
11. Installazione Avvolgitori
12. Installazione Tubi Bowden
13. Installazione Tendini
14. Installazione Scheda
15. Installazione Cover

## 10.7 Registrazione tendini

Per ogni dito che richiede registrazione:
1. Bloccare la mano robotica nella morsa
2. collegare il servomotore nello slot SSI alla scheda elettronica.
3. alimentare la scheda elettronica con un alimentatore a 12V DC che possa erogare fino a 14A, con un connettore unipolare con foro positivo centrale
4. collegarsi via Bluetooth alla scheda logica.
5. inviare via Bluetooth il comando seriale di selezione 'Modalità Installazione Tendini'.
6. aspettare che i servomotori completino il loro movimento e procedere al prossimo punto
7. Per ogni dito che richiede registrazione
1. Svitare di 2 giri il bullone del tendine di estensione usando la chiave esagonale da 2.5mm
2. Svitare di 2 giri il bullone del tendine di flessione usando la chiave esagonale da 2.5mm
3. Assicurarsi che il dito sia completamente esteso, altrimenti estenderlo manualmente
4. Usando la pinza manuale di montaggio con una mano, prendere il tendine di estensione e tirarlo finche non è ben teso
5. Mantenendo il tendine tirato con la pinza manuale di montaggio, con l'altra mano avvitare il bullone di fissaggio finche non è ben stretto (TBD : definire coppia serraggio)
6. Rilasciare il tendine con la pinza manuale di montaggio
7. Assicurarsi che il dito sia completamente esteso sotto effetto del tiraggio del tendine

8. Usando la pinza manuale di montaggio con una mano, prendere il tendine di flessione e tirarlo finche non è ben teso
9. Mantenendo il tendine tirato con la pinza manuale di montaggio, con l'altra mano avvitare il bullone di fissaggio finche non è ben stretto (TBD : definire coppia serraggio)
10. Rilasciare il tendine con la pinza manuale di montaggio

## 11 Pulizia e disinfezione

Le superfici esterne della mano robotica possono essere pulite con:
- un panno leggermente imbevuto d'alcool.
- un panno leggermente imbevuto di amuchina.

NON SPRUZZARE LIQUIDI SULLA MANO ROBOTICA

## 12 Rilevamento dei guasti / risoluzione dei problemi

ANOMALIA | CAUSA
- Dita floscie/oscillanti anche se non mosse dal motore • Dita che chiudono in ritardo • Dita che non chiudono completamente | • tendini non tesi (mano robotica usata oltre i limiti di carico)
- Dita che non aprono completamente • Dita che non chiudono completamente | • calibrazione tendini fallita
- Dita che non si muovono | • tendini danneggiati • tendine staccato • motori danneggiati • interruzione energia elettrica • avvolgitori danneggiati
- Il motori smettono di esercitare forza dopo un certo tempo | • surriscaldamento motori
- Non si puo efftuare un collegamento BlueTooth con la mano robotica | • Distanza troppo grande dal dispositivo controllante o interferenze o ostacoli
- Dita che non fanno presa (grip) sull oggetto | • Pad consumati
- Parti danneggiate o consumate | • Rottura o consumo da usura • Rottura o consumo da uso improprio
CAUSA | SOLUZIONE
- Tendini non tesi | • smontare la cover ed eseguire la registrazione tendini
- Tendini danneggiati | • sostituire i tendini
- Calibrazione tendini fallita | • Riavviare la mano robotica per ripetere la auto-calibrazione. • Spegnere la mano robotica, rimuovere le cover e controllare che i tendini non si siano incastrati tra loro o con altre parti della mano robotica
- Tendini staccati | • Spegnere la mano robotica, rimuovere le cover e riattaccare o sostituire il tendine, poi eseguire la registrazione tendini
- Surriscaldamento motori | • Assicurarsi che la mano robotica venga usato nel corretto range di funzionamento
- Distanza troppo grande dal dispositivo controllante o interferenze o ostacoli | • Avvicinare il dispositivo controllante nel range per il bluetooth (<9m) • Eliminare ostacoli tra il dispositivo controllante e la mano robotica • Eliminare eventuali disturrbi
- Pad consumati | • Sostituire le parti che contengono i pad danneggiati
- Interruzione energia elettrica | • Controllare che l'alimentazione sia attiva e ben collegata • Controllare che i cavi di alimentazione non siano danneggiati
- Rottura o consumo da usura • Rottura o consumo da uso improprio | • Sostituire le parti danneggiate con parti nuove o ricondizionate dal fabbricante

## 13 Smontaggio, disattivazione e rottamazione

## 13.1 Disinstallare la mano robotica

Prima di disinstallare la mano robotica, disattivarlo scollegando il cavo di alimentazione elettrica.

Eseguire in sequenza per smontare la mano robotica dal manipolatore robotico:
- svitare i 4 bulloni M3 che tengono la flangia attaccata alla mano robotica
- staccare la mano robotica dalla flangia
- svitare i 4 bulloni M6 che tengono la flangia attaccata al polso del manipolatore
- staccare la flangia dal polso del manipolatore

## 13.2 Disattivare la mano robotica

Per disattivare la mano robotica, staccare il cavo di alimentazione.

## 13.3 Smontaggio

Prima di smontare la mano robotica, disattivarlo e staccarlo dalla macchina su cui è installato. Per smontare la mano robotica, esequire in sequenza:
- rimuovere le covers della mano robotica
- rimuovere le covers delle dita
- rimuovere il palmo
- rimuovere i bulloni dagli avvolgitori
- rimuovere gli avvolgitori
- rimuovere i tendini con la pinza manuale di montaggio, se necessario tagliarli con le forbici
- rimuovere le dita: indice, medio, anulare, mignolo
- rimuovere la parte flessibile del pollice
- rimuovere la base del pollice
- rimuovere le fascette fermacavo
- rimuovere la barriera-tendini
- rimuovere i motori

## 13.4 Rottamazione

Il prodotto, quando giunge a fine vita, non deve essere smaltito con i rifiuti urbani indifferenziati.

Smaltire secondo la normativa locale sui rifiuti elettrici ed elettronici.

In alternativa, l’utilizzatore può procedere allo smontaggio del prodotto e conferire separatamente le diverse tipologie di componenti secondo le modalità indicate nei paragrafi seguenti e nel rispetto delle normative nazionali e locali in materia di rifiuti.

## 13.5 Componenti elettroniche

Le componenti elettroniche (servomotori, cavi, scheda di controllo) devono essere smaltiti secondo le norme di smaltimento RAEE.

## 13.6 Bulloni, dadi e rondelle

I bulloni, i dadi, le rondelle e le altre piccole parti metalliche, se separati dalle altre componenti, devono essere conferiti nei sistemi di raccolta differenziata dedicati ai metalli o al multimateriale (laddove previsto), secondo le modalità stabilite dal sistema locale di gestione dei rifiuti. L’utilizzatore deve rispettare le normative specifiche vigenti nel proprio Paese e le indicazioni del gestore locale dei rifiuti.

## 13.7 Pad in silicone

Le parti contenenti silicone (dita flessibili, palmo e componenti simili) sono costituite da silicone già catalizzato e non contengono sostanze pericolose note per l’utilizzatore finale.

In assenza di flussi di raccolta dedicati, tali componenti possono essere conferiti come rifiuto urbano indifferenziato, nel rispetto delle norme specifiche vigenti nel proprio Paese e delle indicazioni del gestore locale dei rifiuti.

## 13.8 Parti In plastica rigida

Le parti in plastica rigida (scheletro, base pollice, tubi Bowden, avvolgitori, covers, flangia e componenti simili), se separate dalle parti elettroniche e metalliche, devono essere conferite nei circuiti di raccolta differenziata dedicati alle plastiche o al multimateriale, oppure presso isole ecologiche/centri di raccolta, secondo quanto previsto dal sistema locale di gestione dei rifiuti. L’utilizzatore deve attenersi alle normative nazionali e alle indicazioni del gestore locale in materia di raccolta e riciclo dei rifiuti plastici.

## 13.9 Tendini

I tendini sono realizzati in polietilene ad alta densità (HDPE), una plastica ad alta densità che non deve essere dispersa nell’ambiente.
Tali componenti devono essere conferiti tramite i sistemi di raccolta differenziata per la plastica o presso isole ecologiche/centri di raccolta che accettano rifiuti plastici non pericolosi, secondo quanto previsto dal sistema locale di gestione dei rifiuti. L’utilizzatore deve attenersi alle normative vigenti e alle indicazioni del gestore locale per garantire il corretto recupero o smaltimento di questo materiale.

## 14 Documenti e disegni

## 14.1 Componenti

Componenti:
- scheletro
- dita
- indice con pads in silicone
- medio con pads in silicone
- anulare con pads in silicone
- mignolo con pads in silicone
- pollice con pads in silicone
- servomotori e cavi : 5 x WaveShare ST3215HS
- scheda logica : Waveshare ESP32 Servo Driver Board
- avvolgitori tendini
- tendini in polietilene: marca Hercules 8 strand polietilene, diametro 0.8 mm
- bulloneria
- bulloni M3 a testa svasata
- lunghezza 20mm
- lunghezza 16mm
- bulloni M3 a testa a bottone: lunghezza 10mm
- bulloni M3 a testa svasata con incavo esagonale
- lunghezza 12mm
- bulloni M6
- lunghezza 3.5cm
- viti autofilettanti M2
- lunghezza 6mm
- base pollice
- TRS platform (Thumb Rotatin Servo platform)
- palmo con pads in silicone
- covers
- cover superiore posteriore
- cover inferiore anteriore
- cover inferiore posteriore
- covers falangi dita
- flange di collegamento meccanico
- flangia per robot manipolatore UR3 (per il giunto finale sul polso)

## 14.2 Nomenclatura parti

Nota: i fori sono indicati in rosso.
14.2.1 Nomenclatura fori servomotori pollice

Figure 14.1: Scheletro mano sinistra -vista anteriore - fori servomotori

14.2.2 Nomenclatura fori servomotori dita superiori

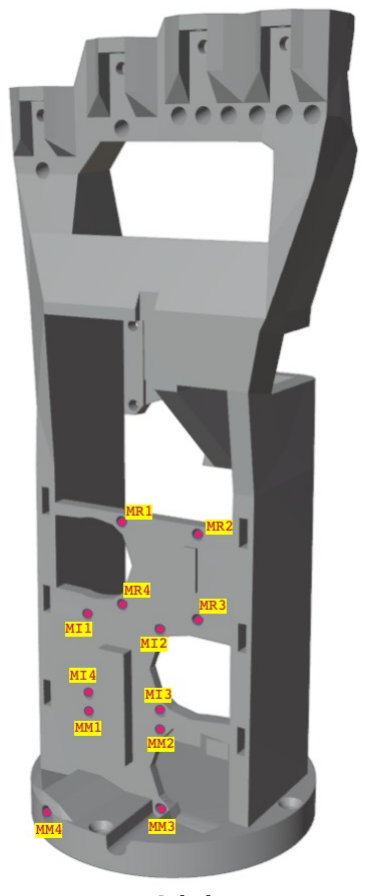
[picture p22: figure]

Figure 14.2: : Scheletro mano sinistra - vista posteriore - fori servomotori

14.2.3 Nomenclatura slot servomotori

Figure 14.3: : Scheletro mano sinistra - vista anteriore - slot motori

14.2.4 Nomenclatura fori flangia servomotore

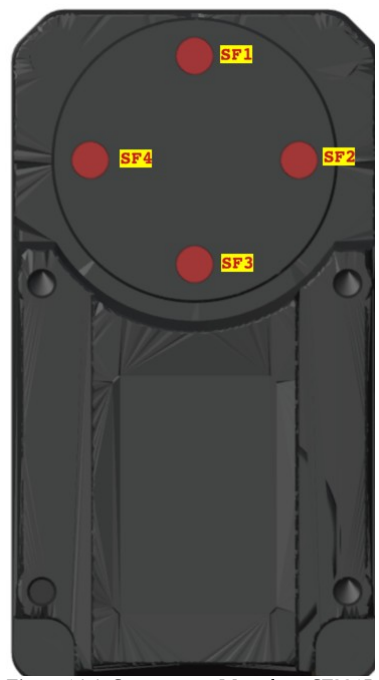
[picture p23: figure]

Figure 14.4: Servomotore Waveshare ST3215 ST3215/HS - fori

14.2.5 Nomenclatura slot e fori dita superiori

Figure 14.5: Mano sinistra - scheletro - vista anteriore - fori e slot dita superiori

14.2.6 Nomenclatura slot e fori base pollice

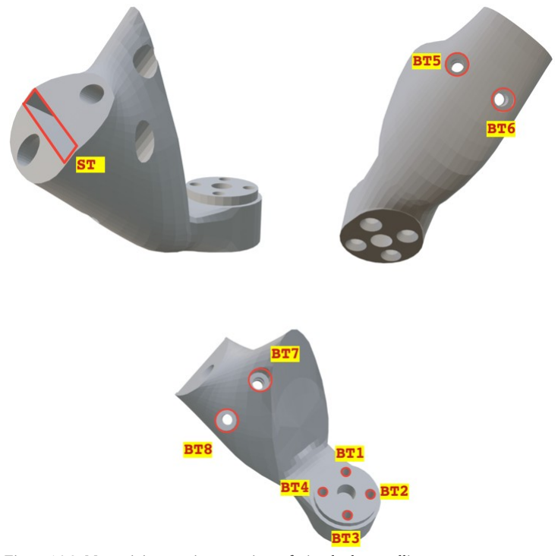
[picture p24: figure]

Figure 14.6: Mano sinistra - vista anteriore - fori e slot base pollice

14.2.7 Nomenclatura fori tendini

Figure 14.8: Mano sinistra - vista
posteriore - fori tendini | Figure 14.7: Mano sinistra - vista anteriore - fori tendini

Figure 14.9: Dito
Indice - Foro
tendine distal - vista
dal basso

Figure 14.10: Dito Indice - Foro tendine distal - vista dall'alto

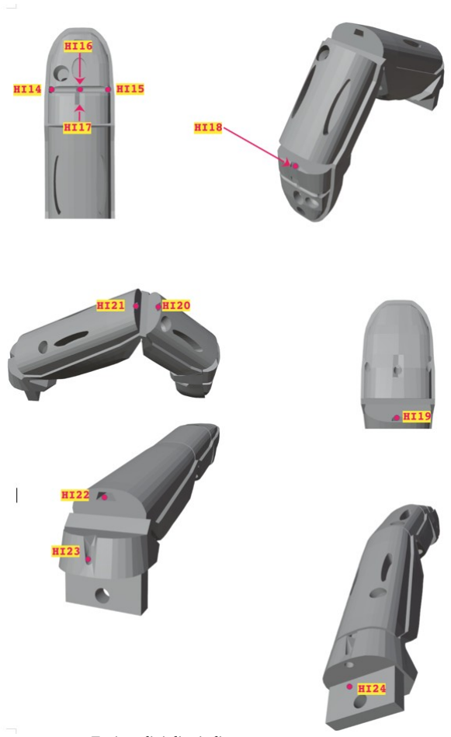
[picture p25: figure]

Figure 14.11: Fori tendini dito indice

Sono mostrati solo i nomi per il dito indice. I nomi dei fori delle altre dita si possono ottenere sostituendo il prefisso HI con quello del dito desiderato. Di seguito riportiamo i prefissi per i nomi delle altre dita superiori (medio, anulare e mignolo).
- Medio: HM
- Anulare: HR
- Mignolo: HL

14.2.8 Nomenclatura fori tendini pollice

Figure 14.12: Fori tendini pollice

14.2.9 Nomenclatura fori avvolgitore

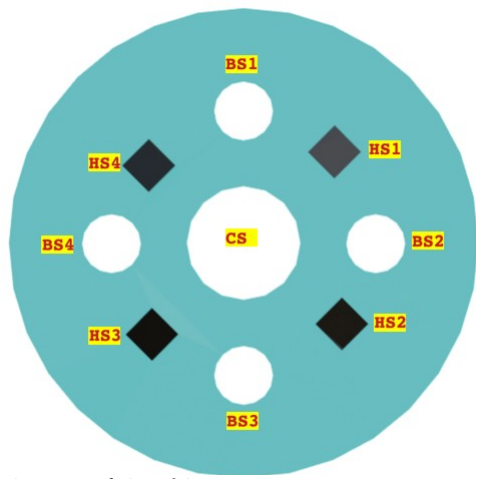
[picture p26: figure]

Figure 14.13: fori avvolgitore

14.2.10 Nomenclatura fori palmo

## TBD

14.2.11 Nomenclatura covers TBD

14.2.12 Nomenclatura fori scheda elettronica TBD

## 15 Rischi residui da trasmettere agli utilizzatori

## 15.1 Avvertenze generali

Questa sezione contiene i rischi residui della quasi-macchina che DEVONO ESSERE COMUNICATI AGLI UTILIZZATORI FINALI nel manuale della macchina completa. L'integratore deve incorporare integralmente questo capitolo.

## 15.2 Rischi meccanici

- Rischio schiacciamento: Le dita robotiche esercitano forza fino a 20N durante la presa. Tenere mani/oggetti lontani durante il funzionamento.
- Tendini scoperti: Rischio aggancio abbigliamento/oggetti esterni. Non toccare i tendini durante il movimento.

## 15.3 Manutenzione obbligatoria (usura normale)

Regolazione tensione tendini (registrazione) è manutenzione ordinaria dovuta a normale usura d'uso, richiesta ogni 5000 cicli (un ciclo = una chiusura dito fino a resistenza, contro palma mano o oggetto)—simile a ritensionamento cavo freno bicicletta. Il mancato rispetto annulla la copertura garanzia. TBD Il firmware registra automaticamente i cicli; controlla l'app per avvisi manutenzione.

## 15.4 Limitazioni operative

- Non operare standalone: La quasi-macchina è pericolosa senza integrazione su robot completo con arresto emergenza e barriere di sicurezza.
- Sovraccarico:
- Pinch grasp: 500 g TBD
- Power grasp: 5 kg TBD
- Lift: 8 kg TBD
- Ambiente: Temperatura 5-40°C, umidità <80% non condensante.

## 15.5 Formazione operatori

Formare operatori su: rischi sopra elencati, procedura registrazione tendini, sezionamento delle enrgie (Cap 10.5)
L'integratore deve tradurre e includere questo capitolo nel manuale end-user della macchina completa.

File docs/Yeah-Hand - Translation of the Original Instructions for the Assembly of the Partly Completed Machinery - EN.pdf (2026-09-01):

Yeah Hand™ – Partly Completed Machinery Assembly Instructions – Rev 1.7 – EN

Yeah Hand™ – Adaptive Electric Robotic Hand – © 2023-2026 Vittorio Lumare

# Assembly Instructions for the Yeah Hand™ Partly Completed Machinery

## Manual for integration, configuration and use by integrators/assemblers Original Instructions

### Company Name: VITTORIO-LUMARE

### Product Name: VITTORIO-LUMARE Yeah Hand™

### Model: Yeah Hand L / Yeah Hand R

### Product Type: Robotic Hand

### Product under development (prototype / partly completed machinery)

intended solely for integrators and beta testers, not for end users.

### Manufacturer's Address:

### Vittorio Lumare

### via Boccioni 4

### 88900 CROTONE (KR)

### Italy

### Revision history

Version | Comment | Author | Date
1.0 | Initial version | Vittorio Lumare | 20/09/2024
1.0 - IT | Italian translation | Fortunato Pantisano | 11/11/2025
1.1 - IT | Translation completed (EU Declaration of Incorporation) | Vittorio Lumare | 11/11/2025
1.2 - IT | EU Declaration of Incorporation and certificates updated | Vittorio Lumare | 11/11/2025
1.3 - IT | Added chapter “Residual risks to be communicated to users” | Vittorio Lumare | 12/01/2026
1.4 - IT | Assembly procedure updated | Vittorio Lumare | 24/06/2026
1.5 - IT | Terms renamed, glossary terms added, sections on components no longer part of the product removed, illustration errors corrected | Vittorio Lumare | 21/07/2026
1.6 – IT | Modified the thumb finger tendon-to-spool installation procedure | Vittorio Lumare | 26/08/2026
1.7 – IT | Converted document from .odt to .docx for AI compatibility; many figures made static for positioning stability | Vittorio Lumare | 27/08/2026

## 1 General notices and machinery conformity

## 1.1 Document structure

## Indice

## 1.2 How to use this manual

We invite readers to first read the safety chapter, which is the most critical and important aspect. Afterwards, it is possible to skip to the desired chapter, each of which can be consulted independently, bearing in mind that each chapter refers to the others via links, so the section of interest can be consulted directly.
The final chapter contains the illustrations with the parts nomenclature, which should be consulted during the assembly procedure.

## 1.3 Legislative references

Directives | Applicable requirements met
Machinery Regulation (EU) 2023/1230 | 1.1.2, 1.1.3, 1.1.5, 1.3.2, 1.3.3, 1.3.4, 1.3.8.1, 1.5.1, 1.5.2, 1.5.5, 1.5.6, 1.6.1, 1.7.1, 1.7.2, 1.7.4, 1.7.4.1, 1.7.4.2, 4.1.2.3, 4.1.2.4, 4.3.1, Annex VI. It is declared that the relevant technical documentation has been compiled in accordance with Part B of Annex IV of the Machinery Regulation. The manufacturer undertakes to transmit, upon reasoned request from national authorities, the relevant technical documentation specified in Annex IV, Part B, within the required time limits.
2014/30/EU Electromagnetic Compatibility (EMC) Directive | Refer to the EMC Directive and the harmonised standards used below.
2011/65/EU Restriction of the use of certain hazardous substances (RoHS) | Refer to the RoHS Directive and the harmonised standards used below.
INTERNATIONAL STANDARD | DESCRIPTION
EN ISO 12100:2010 | 2012 Safety of machinery — General principles for design — Risk assessment and risk reduction
EN 60204-1 | 2009 Safety of machinery – Electrical equipment of machines – Part 1: General requirements
ISO 14539:2000 | Manipulating industrial robots — Object handling with grasp-type grippers — Vocabulary and presentation of characteristics
ISO 14121-2 | ISO/TR Safety of machinery – Risk assessment – Part 2: Practical guidance and examples of methods

## 1.4 Draft EU Declaration of Incorporation

Draft Original EU Declaration of Incorporation

Pursuant to Regulation (EU) 2023/1230, Annex V, Part B, of the European Parliament and of the Council, on machinery,

We, the manufacturer,

VITTORIO-LUMARE via Boccioni 4, 88900 CROTONE (KR) - Italy

We hereby declare that the following product:

Product Name: VITTORIO-LUMARE Yeah Hand

Description: Humanoid Robotic Hand

Functions: Object manipulation, Pick and Place, gestures.

Models: Yeah Hand L, Yeah Hand R

Types: Adaptive Electric Robotic Hand

Serial number:

The partly completed machinery which is the subject of this declaration must not be put into service until the machinery into which it is to be incorporated has been confirmed as being in conformity with the provisions of the Machinery Regulation. Conformity with all essential requirements of the Machinery Regulation depends on the specific robotic application and on the overall risk assessment.

Directives / Regulations | Applicable requirements met
EU Machinery Regulation 2023/1230 | 1.1.2, 1.1.3, 1.1.5, 1.3.2, 1.3.3, 1.3.4, 1.3.8.1, 1.5.1, 1.5.2, 1.5.5, 1.5.6, 1.6.1, 1.7.1, 1.7.2, 1.7.4, 1.7.4.1, 1.7.4.2, 4.1.2.3, 4.1.2.4, 4.3.1, Annex VI. It is declared that the relevant technical documentation has been compiled in accordance with Part B of Annex IV of the Machinery Regulation. The manufacturer undertakes to transmit, upon reasoned request from national authorities, the relevant technical documentation specified in Annex IV, Part B, within the required time limits.
2014/30/EU Electromagnetic Compatibility (EMC) Directive | Refer to the EMC Directive and the harmonised standards used below.
2011/65/EU Restriction of the use of certain hazardous substances (RoHS) | Refer to the RoHS Directive and the harmonised standards used below.

Person responsible for the documentation: Vittorio Lumare. Address: see manufacturer's address.

CROTONE, 07/09/2024 (place and date of issue)

Vittorio Lumare – Technical Director

VITTORIO-LUMARE

The following standards have been applied:

INTERNATIONAL STANDARD | DESCRIPTION
EN ISO 12100:2010 | 2012 Safety of machinery — General principles for design — Risk assessment and risk reduction
EN 60204-1 | 2009 Safety of machinery – Electrical equipment of machines – Part 1: General requirements
ISO 14539:2000 | Manipulating industrial robots — Object handling with grasp-type grippers — Vocabulary and presentation of characteristics
ISO 14121-2 | ISO/TR Safety of machinery – Risk assessment – Part 2: Practical guidance and examples of methods

## 1.5 Incorporated products

Incorporated products
- 5 Servo motors
- Manufacturer: Shenzhen Waveshare Electronics Co., Ltd
- Models: ST3215 Servo, ST3215-HS Servo Motor
- Control logic board
- Manufacturer: Shenzhen Waveshare Electronics Co., Ltd
- Model: Servo Driver with ESP32

Figure 1.1: WaveShare
Servomotor ST3215-HS

Figure 1.2:
WaveShare ESP32
Servo Driver

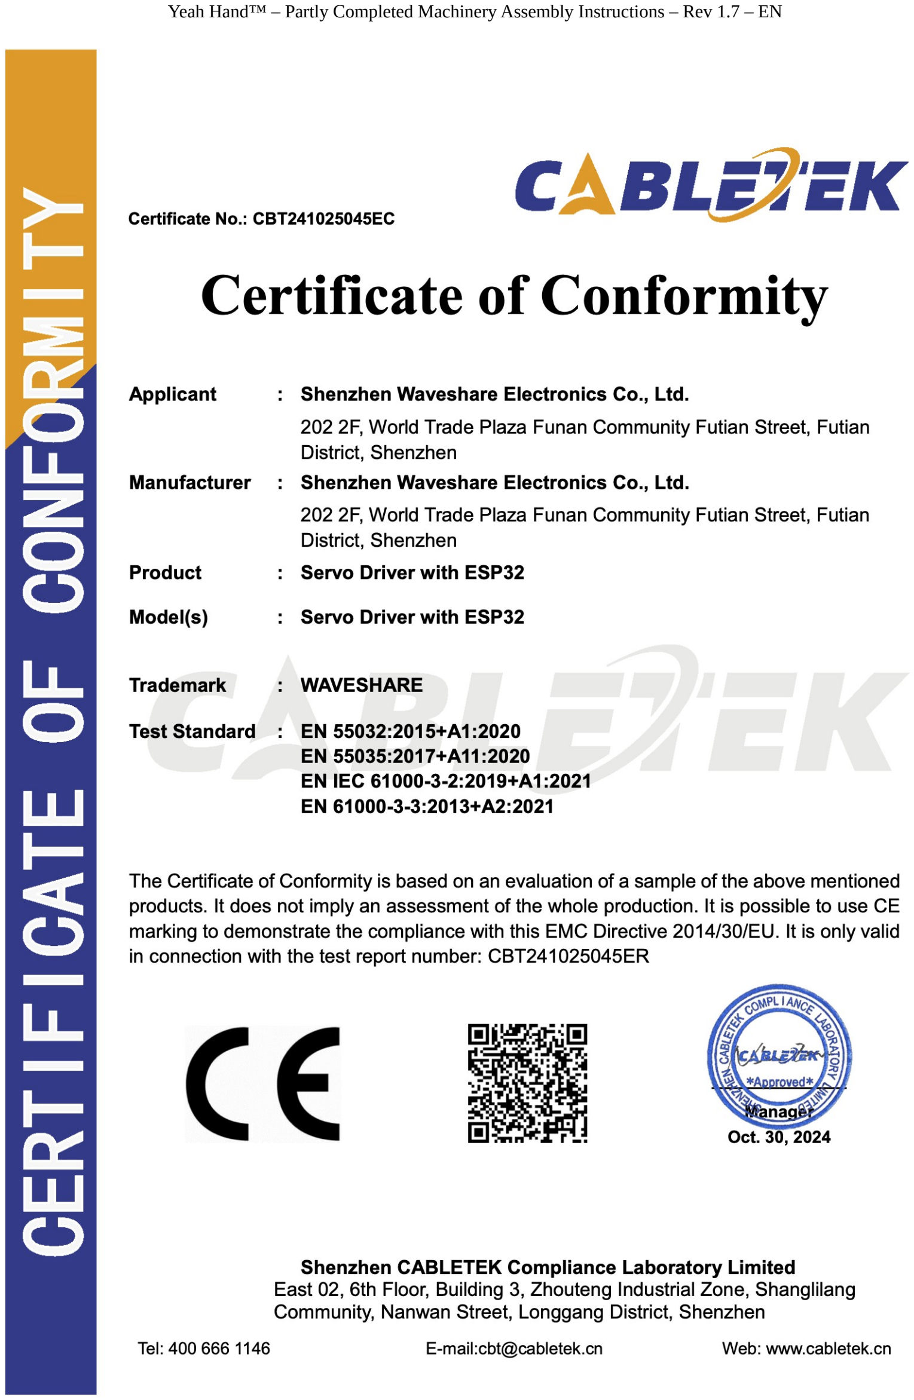
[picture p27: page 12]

## 1.6 Prototype / pre-series nameplate

The final nameplate, including any trademark, will be updated in the final version of the product.

## TO DO INSERT LOGO Manufacturer: VITTORIO-LUMARE

## Model: YEAH-HAND-L / YEAH-HAND-R TBD SN: 2026 000000 Year: 2026

## 2 Safety

## 2.1 Notices concerning hazardous situations

2.1.1 Meaning of symbols
This paragraph explains the meaning of the symbols used throughout the manual. Please read and understand in this chapter the meaning of each symbol.

READ THE INSTRUCTION MANUAL

MANDATORY USE OF THE VICE

MANDATORY USE OF THE ASSEMBLY PLIERS

DO NOT SPRAY LIQUIDS ONTO THE ROBOTIC HAND

DANGER OF FINGER CUTS FROM CABLES

DANGER OF FALLING OBJECTS FROM HEIGHT

DANGER OF OBJECT EJECTION

DANGER OF FIRE

DANGER OF HOT SURFACES

DANGER OF CUTS TO BODY PARTS

DANGER OF CRUSHING OF BODY PARTS

DANGER OF SUBSTANCES HARMFUL TO HEALTH

ELECTRICAL HAZARD

2.1.2 Maintenance operations

!! DO NOT PULL THE TENDONS WITH BARE HANDS !!

MANDATORY
- Use a vice to hold the part being worked on firmly in place
- Use assembly pliers to pull the tendons
POSSIBLE HARM:
- Severe cuts to the fingers
- Blood loss requiring immediate surgery

2.1.3 Putting into service
BEFORE THE PUTTING INTO SERVICE OF THE COMPLETE MACHINE THAT WILL INCORPORATE THE ROBOTIC HAND, THE FOLLOWING SYMBOLS MUST BE AFFIXED TO THE FINAL PRODUCT, SO THAT THEY ARE ALWAYS VISIBLE TO POSSIBLE PERSONS IN THE VICINITY

2.1.4 Typical operation
2.1.4.1 Persons near the robotic hand

WARNING: the robotic hand could break during use!
POSSIBLE HARM: if the robotic hand breaks, some broken parts could be sharp or pointed and could cut people's skin and cause permanent injury or blood loss and/or require immediate surgical intervention

2.1.4.2 Robotic hand holding an object

WARNING: an object could detach from the robotic hand and strike a person
POSSIBLE HARM: A thrown object could cause: breakage of bones, cuts or stab wounds, burns if very hot, contamination if it contains or is made of harmful substances.

2.1.4.3 Interaction with persons

WARNING: fingers or human skin can become trapped in the mechanisms and be injured POSSIBLE HARM: a finger can be crushed to the point of causing severe bruising to skin or nails, a tendon can cut a human finger to the point of causing blood loss and/or require immediate surgical intervention, sharp parts can cut skin causing bleeding or bruising.

2.1.5 Hazardous situations and residual risks

Hazardous Situation | Hazardous Event | Hazard | RESIDUAL RISKS AFTER IMPLEMENTATION OF REDUCTION MEASURES
Handling the tendon wires | Contact of human fingers with a tendon pulled under force | Cutting or abrasion of human fingers by the tendon wires | Skin injury if the operator does not follow the instructions during:• removal/insertion of the tendon •

2.1.6 Permitted use of the machine and residual risks

Hazardous Situation(ISO 12100:2010, Table B.3) | Hazardous Event(ISO 12100:2010, Table B.4) | Hazard(ISO 12100:2010, Table B.1) | RESIDUAL RISKS AFTER IMPLEMENTATION OF REDUCTION MEASURES
Being near the robotic hand's working area (depends on the complete machine incorporating the robotic hand) | The robotic hand breaks during operation, exposing sharp or abrasive parts | Impact, puncture, stabbing, abrasion | On the complete machine, incorporating the robotic hand, manufactured by others, one of these risks is possible:• A broken part may be sharp and cut human skin, causing bleeding and requiring immediate surgery.
Being at a distance sufficient to be struck by an object held by the robotic hand, should the object detach from the robotic hand for any reason | Contact with an object ejected/thrown from the robotic hand | Impact, abrasion, cut, stabbing, puncture, burn, electrocution or contamination from hazardous substances caused by an ejected/thrown object | On the complete machine, incorporating the robotic hand, manufactured by others, one of these risks is possible:• A thrown object may cause: bone fractures, cuts or cutting wounds if sharp, burns if hot, contamination if it contains or is made of harmful substances.
Intensive use of the robotic hand | Flame generated by overheated motors or the electronic board | Flame | On the complete machine, incorporating the robotic hand, manufactured by others, one of the following risks is possible:• The robotic hand may catch fire if used intensively beyond its limits.

2.1.7 Non-permitted use of the machine and residual risks
During permitted use of the robotic hand, once integrated into the final machine, the following hazardous situations may occur:
Hazardous Situation | Hazardous Event | Hazard | RESIDUAL RISKS AFTER IMPLEMENTATION OF REDUCTION MEASURES
Being near the robotic hand's working area (depends on the complete machine incorporating the robotic hand) | Contact with harmful parts of the held object: sharp edges, points, abrasive surfaces | Puncture, stabbing, abrasion, burn, electrocution | Puncture, stabbing, abrasion, burn, electrocution
Being near the robotic hand's working area (depends on the complete machine incorporating the robotic hand) | Contact with a heavy object | Impact | Impact
Being near the robotic hand's working area (depends on the complete machine incorporating the robotic hand) | Contact with the high-temperature part of the held object | Burns | Burns
Being near the robotic hand's working area (depends on the complete machine incorporating the robotic hand) | Contact with the high-voltage part of the held object | Electrocution, burn | Electrocution, burn
Being near the robotic hand's working area (depends on the complete machine incorporating the robotic hand) | Contact with a held object contaminated by hazardous substances | Contamination by hazardous substances from part of the held object | Contamination by hazardous substances from part of the held object

It is important that integrators reduce the above risk situations, as they depend on the final machine and the associated risks cannot be reduced by acting on the robotic hand alone.

The following hazardous situations have been analysed and the related risks reduced by the manufacturer; they nonetheless still present residual risks.

Hazardous Situation(ISO 12100:2010, Table B.3) | Hazardous Event(ISO 12100:2010, Table B.4) | Hazard(ISO 12100:2010, Table B.1) | RESIDUAL RISKS AFTER IMPLEMENTATION OF REDUCTION MEASURES
Touching the robotic hand's phalanges with human fingers | Contact of human fingers with moving parts of the robotic hand | Crushing of very small human fingers in the space between the robotic finger and the tendon, cutting of human fingers via forceful tendon traction | On the complete machine, incorporating the robotic hand, manufactured by others, one of these risks is possible:• The finger may be compressed to the point of causing severe bruising to skin or nails• The tendon may cut the human finger to the point of causing bleeding and requiring surgery
Touching the palm of the robotic hand | Contact of human fingers with moving | Crushing of human fingers or skin in | On the complete machine, incorporating the robotic hand,

| parts of the robotic hand | the space between the thumb base and the palm or skeleton | manufactured by others, one of these risks is possible:• The finger may be compressed to the point of causing severe bruising to skin or nails
Being under the robotic hand while it is holding an object | Object falling | Impact from a falling object | On the complete machine, incorporating the robotic hand, manufactured by others, one of these risks is possible: • A falling object may cause: bone fracture, cuts or stab wounds if sharp, burns if hot, contamination if contaminated
Touching an overheated robotic hand | Burn caused by contact with the flame generated by the robotic hand or by the overheated robotic hand | Burns | On the complete machine, incorporating the robotic hand, manufactured by others, one of these risks is possible:Skin burns caused by flames •
Being at a sufficient distance from a damaged robotic hand to be struck by an object held by the damaged robotic hand, should the object detach from the damaged robotic hand for any reason | Contact with an object ejected/thrown from the damaged robotic hand | Impact, abrasion, cut, stabbing, puncture, burn, electrocution or contamination from hazardous substances by an ejected/thrown object | On the complete machine, incorporating the robotic hand, manufactured by others, one of these risks is possible:A falling object may cause: bone fractures, cuts or cutting wounds if sharp, burns if hot, contamination if contaminated.A thrown object may cause: bone fractures, cuts or cutting wounds if sharp, burns if hot, contamination if it contains or is made of harmful substances.A broken part may be sharp and cut human skin, causing bleeding and requiring immediate surgery. • • •

## 2.2 Personal protective equipment

2.2.1 Protective equipment for assembly and maintenance

During assembly and maintenance operations, it is mandatory to use the following tools:
- Assembly pliers to hold and pull the tendons
- Vice to hold the robotic hand firmly in place during the operation

2.2.2 Protective equipment for permitted use
During permitted use of the robotic hand, no special protective equipment is required.
It is the responsibility of integrators to analyse further risk situations during use of the complete machine, and to add any appropriate protective equipment.

## 2.3 Warning plates affixed to the machine

These symbols must be affixed to the complete machine so that they are visible to the operators of the machine:

These symbols must be affixed to the complete machine before it is put into service, visible to anyone within the range of the complete machine to anyone, operators or simple passers-by or visitors:

This symbol must be affixed to the complete machine before it is put into service, visible to anyone within range of the complete machine, to anyone, operators, passers-by, or visitors, only where the complete machine incorporating the robotic hand is used to handle objects containing substances hazardous to health

## 2.4 Emergency situations

In case of fire, disconnect the power supply.
In case of contamination by hazardous substances, the integrators who manufactured the complete machine handling such substances, must carry out a risk analysis and assess emergency situations and record them in the technical file and in the instructions of the complete machine.

## 3 Machine overview

## 3.1 Machine description

Manufacturer | VITTORIO-LUMARE
Machinery Type | Robotic Hand (PARTLY COMPLETED MACHINERY)
Hand Model | Yeah Hand L (Left Hand), Yeah Hand R (Right Hand)The left-side model resembles the human "left" hand.The right-side model resembles the human "right" hand.
Type of robotic hand | Adaptive Electric Robotic Hand
Main applications of the robotic hand | Service robotics:• Grasping/releasing objects• Pick and place• Use of panel controls• Use of mechanical buttons• Hand gestures for human-robot interaction

Overall Technical Drawing - External View

Detailed Technical Drawing - Internal View

Detailed Technical Drawing - Measures


Detailed Technical Drawing

Detailed Technical Drawing

Detailed Technical Drawing

Detailed Technical Drawing

## 3.2 Intended use

This electric robotic hand is adaptive and is designed for robotic applications. The robotic hand must be installed on a handling device, such as:
- a mobile platform
- a robotic manipulator
- a humanoid service robot
- a non-humanoid service robot

The robotic hand is suitable for applications:
- educational:
- schools
- universities
- research:
- laboratories
- research centres
- universities
- prototyping:
- development of service robots (humanoid or otherwise) incorporating the robotic hand
- commercial
- integrated into service robots:
- in public areas
- for domestic use
- hobbyist

The robotic hand is not suitable for industrial applications, as it does not possess sufficient:
- robustness
- repeatability
- high immunity to disturbances typical of industrial environments

## 3.3 Reasonably foreseeable misuse

Misuse situations:
- coming into physical contact with living beings
- handling of skin or body parts
- shaking hands with persons or animals
- highly humid environments, or with water droplets or high-density vapours
- temperatures above 50 ˚C
- lifting objects heavier than 2kg
- handling substances hazardous to health, radioactive, or at high temperature (above 50 degrees)
- handling liquids or powdery substances, or with small particles (under 12 mm)

## 3.4 Technical characteristics of the machine

Robotic hand performance
Mass of the robotic hand (kg) | 650g without covers / 750g with covers
Maximum distance between fingers (mm) | 160 mm
Minimum distance between fingers (mm) | 0
Maximum grip force (N) | 90N (TBD : calculated)
Maximum manipulation force (N) | 35N (TBD : calculated)
Maximum allowable finger moment (N*m) | 0.1
Grip surface (mm2) | 1260
Operating time: Grasp (s) | 2
Operating time: Release (s) | 2

Type of robotic hand
Number of fingers | 5
Finger arrangement | Humanoid
Degrees of mobility of the hand (4.3.1) | Spatial grasp: 6
Degrees of freedom of the hand (4.3.2) | 5
Type of grasp (4.3.6) | 4.3.6.2 non-centric grasp4.3.6.3 adaptive grasp4.3.6.5 asymmetric grasp4.3.6.6 grasp force

Fingers
Degrees of mobility per finger (4.4.1) | Index: 3Middle: 3Ring: 3Little: 3Thumb: 5
Degrees of freedom per finger (4.4.2) | Index: 1Middle: 1Ring + Little: 1Thumb: 2
Finger movement (4.4.3) | • Index: multi-articulated fingers (4.4.3.3)mechanically independent fingers (4.4.3.6)Middle:multi-articulated fingers (4.4.3.3)mechanically independent fingers (4.4.3.6)Ring:multi-articulated finger (4.4.3.3)mechanically interconnected finger (4.4.3.6)Little:multi-articulated finger (4.4.3.3)mechanically interconnected finger (4.4.3.6)Thumb:multi-articulated fingers (4.4.3.3)mechanically independent fingers (4.4.3.6) ◦ ◦ •

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
Actuators (4.2.1.4)
Actuator type | Electric motors
Number of actuators | 5
Rated actuator power (W) | 60W

Power transmission mechanisms (4.2.1.5)
Upper finger mechanism (index, middle, ring, little) | Gear + cable
Thumb flexion mechanism | Gear + cable
Thumb rotation mechanism | Gear
Note: "cable" refers to the tendon, a braided polyethylene fishing line

Finger movement details (referenced to the mechanical interface coordinate system as defined in ISO 9787):
TCP definition (3.3.8): offset from the XmYm plane | Zoffset = 146.1 mm
TCP definition (3.3.8): offset from the Zm axis | Xoffset = -0.1 mmYoffset = 18.9 mm

Finger control
Finger control scheme (4.5) | 4.5.6 Hybrid Control
Control signals | Wireless serial character commands (BT, WiFi)Signal 1: Select ModeTendon InstallationTendon CalibrationRelax (no movement)Grasp Control (POWER, POWERSMALL, MONKEY, PINCH)RAW Control (full control of each finger joint)Signal 2: Fingers Closed/Open: 0-100% • ◦ ◦ ◦ ◦ ◦ • ◦
Feedback signals | Wireless serial characters (BT, WiFi)Position: integer valueSpeed: integer valueLoad: integer valueTemperature: integer valueCurrent: integer valueMovement: integer value (0: false, 1: true)Status: integer value •

•
•
•
•
•
•

Finger control block diagram

Sensing functions (3.4)
Position sensing | Yes: Resolution: 4096, Range: [0, 360] degrees
Torque sensing | Yes: Resolution: 2000, Range: [-25, 25] Kg*cm
Temperature sensing | Yes: Accuracy: 1˚C, Range: [0, 70]˚C
Voltage sensing | Yes: Accuracy: 0.1V, Range: [0, 12]V
Current sensing | Yes (TBD)
Movement sensing | Value: 1: Moving, 0: Stationary

Clamping elements (4.6)
Material | • Rigid polymer (e.g. ABS / PLA / PETG / nylon)Flexible
| polymer (e.g. TPU / TPE)Skin-safe silicone (e.g. Smooth‑On Dragon Skin NV / Reschimica R PRO GLASS)
| •
| •

pu : user desired positionpin : controller C commanded positionpout : real output positionlout : real output loadC : Gripper main controllerSCL: Servomotor Control Loop (inside the servomotor)

Replaceable | Yes
Interchangeable | Yes

Operating environment
Temperature range | 10 – 40 ˚C
Relative humidity range | 0 – 80 %
IP protection | IP20 (INSUFFICIENT, MUST BE >IP4X)

Object properties
Geometry (shape, dimensions) (mm) | Shape: any shape Dimensions: maximum diameter 10 cm
Object mass (kg) | 0 - 2 kg TBD
Max/min object temperature (˚C) | 10˚C - 40˚C
Surface characteristics | Anything free of: sharp edges/points, abrasive surfaces, harmful substances, liquids, radioactive materials
Magnetic properties | < 1T

Robotic interfaces (4.7) and wrist mechanisms:
Mechanical interface | Compliant with standard | UNI EN ISO 9409-1:2005
| Designation code | ISO 9409-1-50-4-M6
Functionality (power and signal transmission) | Power transmission: direct current 12 V, max 14 ANo signal transmission through the robot interface (transmission is wireless)

Warning
Risk (in the final machine) of: crushing, puncture, cutting, stabbing, fire, burn

## 3.5 Controls and signalling

The robotic hand includes no physical controls; it is equipped with a wireless serial Bluetooth character interface.
Implementation of any controls is the responsibility of the integrators of the complete machine.

## 3.6 Environmental limits of the machine

Operating environment
Temperature range | 10 – 40 ˚C
Relative humidity range | 0 - 80
IP protection | TBD: IP40

## 4 Transport, handling and storage

## 4.1 Transport

The robotic hand may be transported by hand.
It is recommended to transport the robotic hand in packaging that prevents:
| • impact with surfaces that could compromise the structural integrity or the finish of the external surfaces. • the ingress of liquids or dust, or of materials smaller than 12 mm TBD

It is recommended to remove the robotic hand from the machine on which it is integrated before transporting it, as it could be damaged during transport.
During transport, the temperature must not exceed 70 ˚C, otherwise geometric alterations of the materials it is made of may occur.
IMPORTANT: Before transporting the robotic hand, disconnect the power supply!

## 4.2 Handling

It is recommended to use a robotic manipulator to handle the robotic hand.

## 4.3 Storage

The robotic hand may be stored under the following conditions:
| • temperature ◦ 5˚C - 40˚C • humidity : ◦ 0 - 70% RH • light: ◦ store in the dark in a closed box ◦ do not expose to UV rays

## 5 Assembly

These instructions explain how to assemble the robotic hand starting from its already manufactured components.

## 5.1 Servo motor installation and registration

This section describes how to install the servo motors in the hand's skeleton and how to register them on the logic board to ensure correct operation.

Figure 5.1: Left Hand - Skeleton - Rear View – no components mounted


Figure 5.2: Left Hand - Skeleton -Front View – no components mounted

5.1.1 Installing the Thumb Base and Thumb Rotation Servo motor (20 min)
Note: TRS is an acronym for Thumb Rotation Servo
Installation:
1. Install the Thumb Base onto the TRS flange (4 M3 bolts, 16 mm long) as shown in figure 5.3.
2. Install the TRS onto the TRS Platform as shown in figure 5.4 and secure with 4 M3 self-tapping screws, max 6 mm long (DO NOT use longer screws, or the servo motor will break)
3. Insert the assembled TRS Platform+Thumb Base onto the skeleton as shown in figure 5.5 and secure with 4 M2 bolts, 5 mm long.

Figure 5.3: Thumb Base on the Thumb Rotation Servomotor

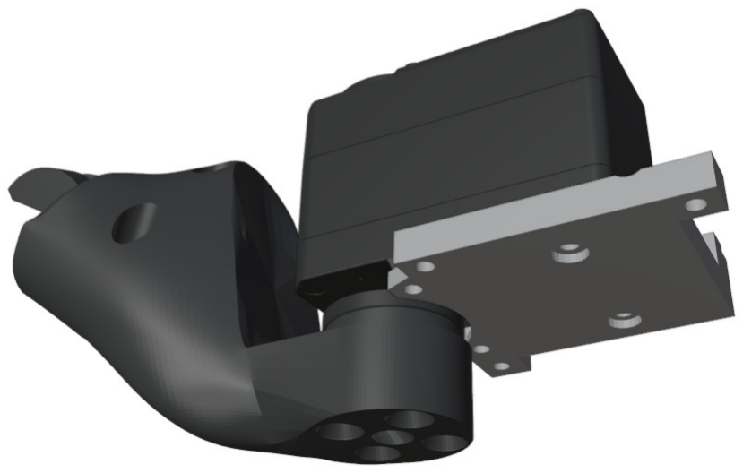
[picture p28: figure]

Figure 5.4: Thumb Base and TRS on TRS Platform

Figure 5.5: TRS and TRS Platform installed on the skeleton

5.1.2 Installing the 4 finger-flexion servo motors (15 min)
Note: each flexion servo motor (there are 4) must be secured in its slot using 4 M2 self-tapping screws, 6-8 mm long.
1. Install each servo motor in its slot as shown in figures 5.5 and 5.6
2. Screw the servo motor to the skeleton holes using the four screws provided.
3. WARNING: Use the screwdriver provided and tighten the screws lightly to avoid damaging the servo motor's threaded seat, which is very delicate.
1. Note for the lowest servo motor (the one at the base of the skeleton):
1. remove the central screw of the rotating flange to allow insertion into the slot.
2. connect 2 control cables to the servo motor, as it will not be possible to insert them afterwards.
3. Insert the servo motor into the slot
4. Re-tighten the central screw on the flange.
4. Make sure that all servo motor control cables are disconnected except for those of the lowest servo.

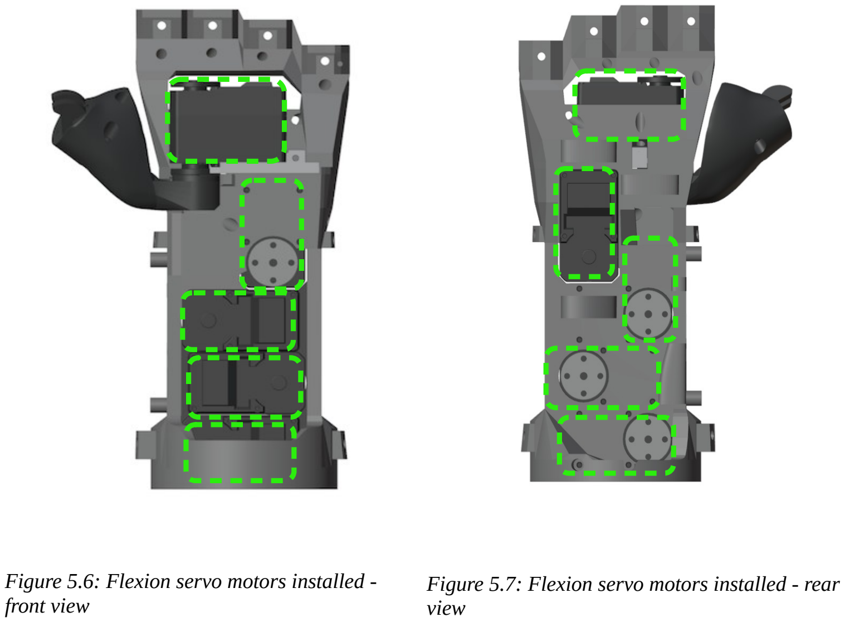
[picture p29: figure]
front view; view

Figure 5.6: Flexion servo motors installed -Figure 5.7: Flexion servo motors installed - rear

5.1.3 Servo motor registration and calibration

Before starting:
- Make sure the logic board is
- removed from the hand
- powered off and disconnected from both the power supply and the USB cable.
- Disconnect all servo motors from the logic board.

Procedure (for each flexion servo motor):
1. Connect the logic board to the PC via USB cable.
2. Upload the program corresponding to the servo motor (table 5.1).
3. Once uploading is complete, disconnect the USB cable.
4. Important: never power the board with the USB cable connected and the external power supply connected at the same time.
5. If the servo motor is a flexion servo (finger bending via tendons):
1. Screw a bolt into one of the holes of the circular plate.
2. Rotate the plate until the hole with the bolt is at the bottom right (figure 5.9).
6. If the servo motor is the thumb rotation servo:
1. Position the thumb at approximately the middle of the range (figure 5.8).
7. Connect the servo motor to the logic board (leave all others disconnected).
8. Power the logic board with the power connector (not with the USB cable!)
9. The program automatically performs:
1. registration of the servo motor ID
2. registration of the central position of the range
3. 4 oscillations of the plate at the end of the procedure (to confirm success)
10. Important: Power off the logic board by disconnecting the power supply.
11. Important: Disconnect the servo motor from the logic board.

TABLE 5.1: Servo motor / Registration program (for the logic board)
Servo motor | Registration program
Thumb Rotation | Thumb Rotation Registration Program
Thumb Flexion | Thumb Flexion Registration Program
Index Flexion | Index Flexion Registration Program
Middle Flexion | Middle Flexion Registration Program
Ring Flexion | Ring Flexion Registration Program
Note: the little-finger servo motor is not present because it is controlled by the ring-finger motor.

Figure 5.9: Flexion servo

motor registration5.9 | Figure 5.8: Thumb rotation servo motor registration5.8

## 5.2 Programming the logic board with the operating program

Once the servo motors have been registered, the board must be programmed with the robotic hand's operating program. The program is 'RebeliaRobot'.
1. DISCONNECT THE SERVO MOTORS FROM THE BOARD
2. Open Arduino IDE
3. Select the board: ESP32-WROOM-DA Module
4. Open the RebeliaRobot.ino program
5. Disconnect the power connector from the logic board
6. Connect the logic board to the PC with the USB cable
7. Upload the program from Arduino IDE
8. Wait for the operation to complete
9. Disconnect the USB cable from the logic board
10. Connect the power connector to the logic board

5.2.1 Servo motor connection
The servo motors are connected to the logic board in a daisy chain, see figures 5.10 and 5.11.
1. Connect the logic board to servo motor 2
2. Connect servo motor 2 to servo motor 3
3. Connect servo motor 3 to servo motor 1
4. Connect servo motor 1 to servo motor 4, first passing the cable into cavity S1 and out through cavity S2
5. Connect servo motor 4 to servo motor 5, passing the cable into cavity S3
At this point, all servo motors are connected to the logic board in a daisy chain.

Figure 5.10: Front view. ID Servomotors, logic board PCB and cavity S1 e cavita S1

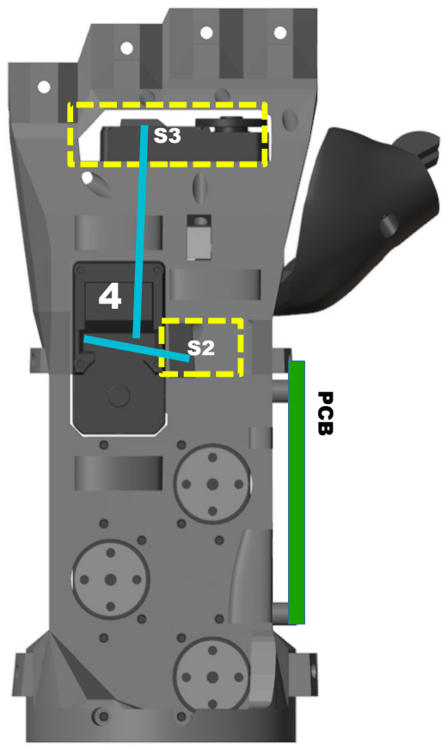
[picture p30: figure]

Figure 5.11: Rear view. ID Servomotors, logic board PCB and cavity S2 e cavita S2

## 5.3 Installing the logic board

1. Install the logic board onto the skeleton as shown in figure 5.12, using 4 M2 self-tapping screws, 6 mm long.

Figure 5.12: Logic board installed5.12

## 5.4 Installing the tendons in the fingers

5.4.1 Installing tendons in the upper fingers

WARNING: the tendons can
cut fingers!

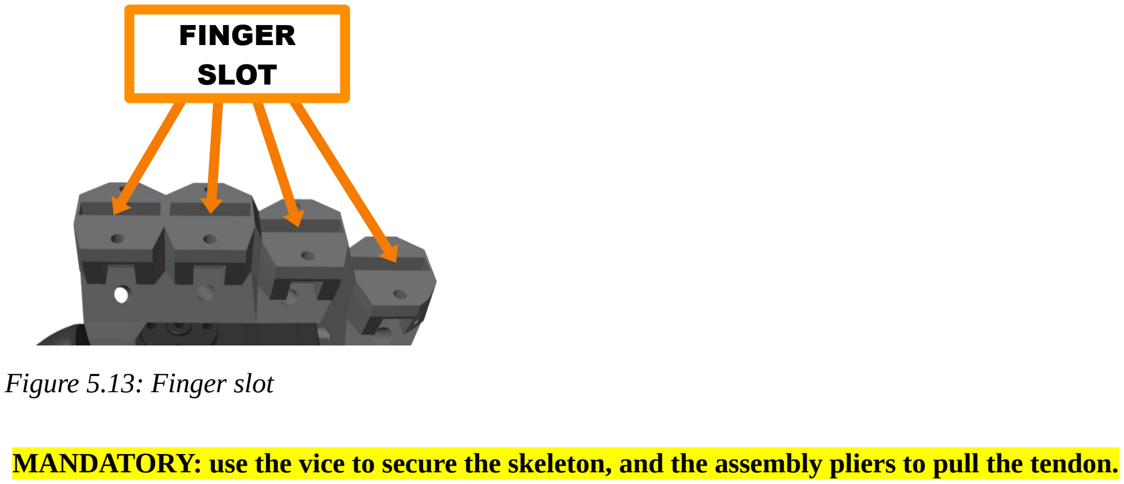
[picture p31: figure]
Figure 5.13: Finger slot; FINGER SLOT

MANDATORY: use the vice to secure the skeleton, and the assembly pliers to pull the tendon.

Installing the tendon for the index finger (the same procedure also applies to the middle, ring and little fingers):
Note: at present, the assembly kit is supplied with the tendons already installed on the fingers.

5.4.2 Installing the tendon in the thumb

WARNING: the tendons can
cut fingers!
MANDATORY: use the vice to secure the skeleton, and the assembly pliers to pull the tendon.

Note: at present, the assembly kit is supplied with the tendons already installed on the fingers.

## 5.5 Installing the Index, Middle, Ring and Little fingers

Note: each finger must be secured in its slot on the skeleton with an M3 10mm bolt.
1. Insert the finger into its slot on the skeleton (figure 5.13)
1. leave the tendons out; they will be inserted into the skeleton holes later, in another procedure
2. Position the nut in its seat on the front of the skeleton (figure 5.14)
3. Secure the nut with the provided insertion tool (figure 5.16)
1. Note: the tool is also used to hold the nut steady in its hexagonal seat while the bolt is being tightened
4. Insert the bolt into the hole on the rear of the skeleton and tighten it (figure 5.15)

Figure 5.14: Nut seat

### NUT SEAT

Figure 5.15: Finger bolt insertion

Bolt

Figure 5.16: Nut
insertion and holding
tool

## 5.6 Installing the Thumb finger

Note: the thumb must be secured in its slot on the thumb base with two M3 countersunk bolts, one 16mm long and one 20mm long.
1. Insert the finger into the slot (figure 5.17)
2. Insert two bolts from behind (figure 5.17)
1. Bolt 1: M3 countersunk, 16 mm long
2. Bolt 2: M3 countersunk, 20 mm long
3. Secure with two M3 nuts placed on the opposite side (figure 5.18)

Figure 5.17: Thumb slot and bolt slots; THUMB SLOT; BOLT SLOT 1 (16mm); BOLT SLOT 2 (20 mm); Figure 5.18: Thumb fastening with nuts; NUT SEATS

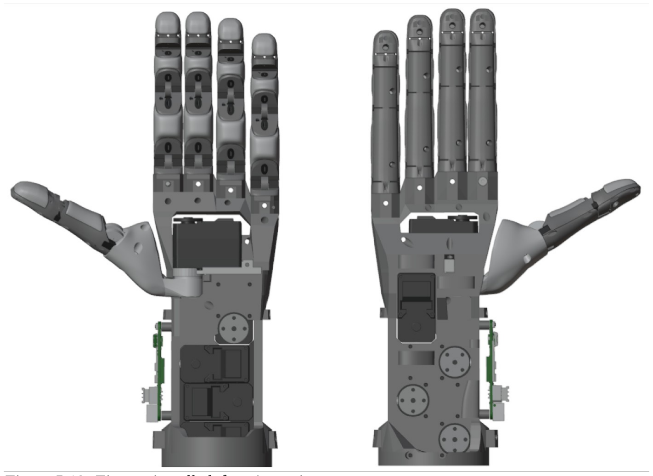
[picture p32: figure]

Figure 5.19: Fingers installed, front/rear view

## 5.7 Installing the Bowden tubes

5.7.1 Installing the Bowden tube for the Index finger

For the INDEX finger only:
1. Flexion tendon:
1. Insert the PTFE tube into the outlet hole (on the rear of the skeleton) of the flexion tendon (figure 5.20), let it come out through the inlet hole on the front of the skeleton and insert it into the initial slot (figure 5.22)
2. Take the remaining part (on the rear of the skeleton) and insert it into the final slot shown in figure 5.21.
3. Note: if the tube is too long, shorten it by cutting it with a utility knife.
2. Extension tendon:
1. Insert one end of the PTFE tube into the initial slot (on the rear of the skeleton) of the extension tendon (figure 5.24)
2. Insert the other end into the final slot shown in figure 5.23: if the tube is too long, shorten it by cutting it with a utility knife.

Figure 5.20: Inserting the tube into the tendon outlet hole (rear view)

Figure 5.21: Inserting the tube into the initial slot (front view)

Figure 5.22: Inserting the tube into the final slot (rear view)

Figure 5.24: Inserting the tube into the initial slot (rear view)

Figure 5.23: Inserting the tube into the final slot (rear view)

FINAL SLOT

5.7.2 Installing the Bowden tube for the Middle finger

For the MIDDLE finger only:
1. Flexion tendon:
1. Insert the PTFE tube into the outlet hole (on the rear of the skeleton) of the flexion tendon (figure 5.26), let it come out through the inlet hole on the front of the skeleton and insert it into the initial slot (figure 5.27)
2. Take the remaining part (on the rear of the skeleton) and thread it first through the 2 pass-through tunnels and then into the final slot (figure 5.25).
3. Note: if the tube is too long, shorten it by cutting it with a utility knife.
2. Extension tendon:
1. Insert one end of the PTFE tube into the initial slot (on the rear of the skeleton) of the extension tendon (figure 5.28)
Insert the other end into the final slot shown in figure 5.29
2. Note: if the tube is too long, shorten it by cutting it with a utility knife.

Figure 5.26 : Inserting the tube into the two pass-through tunnels and then into the final slot (rear view); TUNNEL; FINAL SLOT

Figure 5.27: Inserting the tube into the tendon outlet hole (rear view)

Figure 5.25: Inserting the tube into the circular slot (front view)

INITIAL SLOT

Figure 5.29 : Inserting the tube into the initial slot (rear view)

Figure 5.28 : Inserting the tube into the final slot (rear view)

FINAL SLOT

5.7.3 Installing the Bowden tube for the Ring finger

For the RING finger only
1. Flexion tendon:
1. Insert the PTFE tube into the outlet hole (on the rear of the skeleton) of the flexion tendon (figure 5.31), let it come out through the inlet hole on the front of the skeleton and insert it into the initial slot (figure 5.32)
2. Take the remaining part (on the rear of the skeleton) and thread it first through the pass-through tunnel and then into the final slot (figure 5.30).
3. Note: if the tube is too long, shorten it by cutting it with a utility knife.
2. Extension tendon:
1. Insert one end of the PTFE tube into the initial slot (on the rear of the skeleton) of the extension tendon (figure 5.34)
2. Insert the other end into the pass-through tunnel and then into the final slot (figure 5.33).
3. Note: if the tube is too long, shorten it by cutting it with a utility knife.

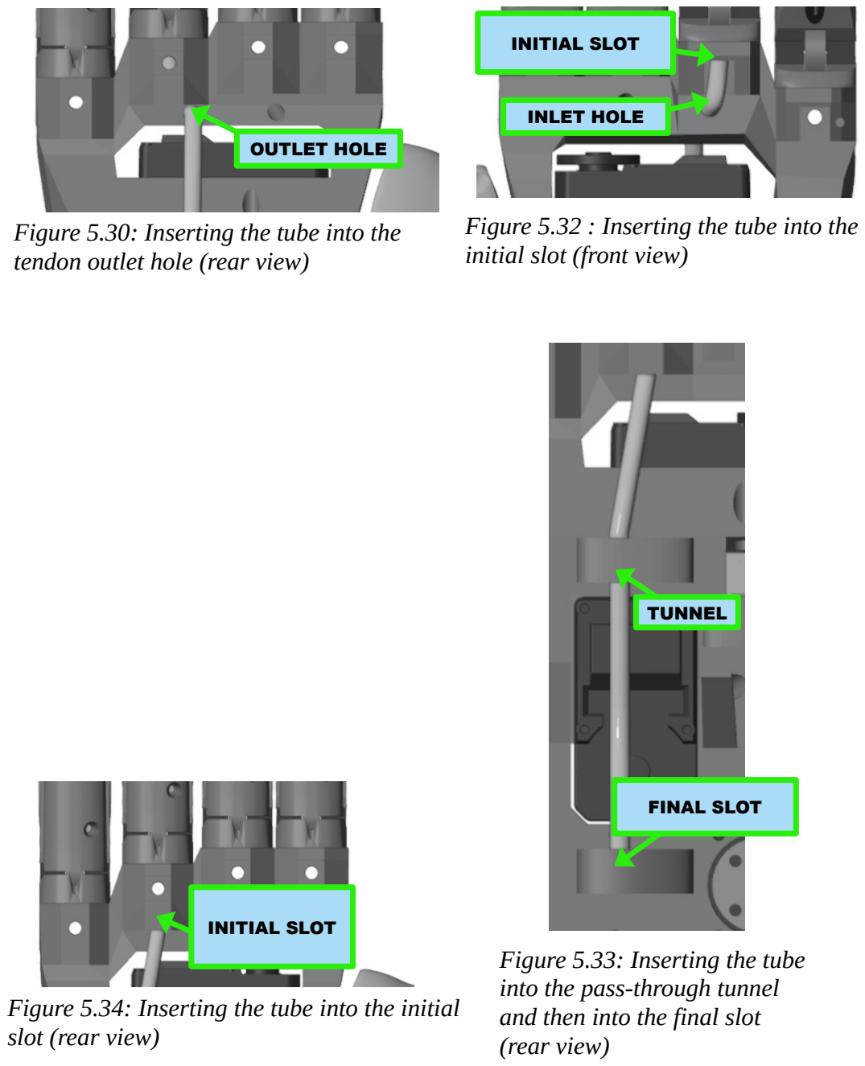
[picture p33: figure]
tendon outlet hole (rear view); OUTLET HOLE; initial slot (front view); INLET HOLE; INITIAL SLOT; slot (rear view); Figure 5.33: Inserting the tube into the pass-through tunnel and then into the final slot (rear view); FINAL SLOT; TUNNEL

Figure 5.30: Inserting the tube into the

Figure 5.32 : Inserting the tube into the

Figure 5.31: Inserting the tube into the pass-through tunnel and then into the
final slot (rear view) (vista posteriore)

Figure 5.34: Inserting the tube into the initial

5.7.4 Installing the Bowden tube for the Little finger

For the LITTLE finger only
1. Flexion tendon:
1. Insert the PTFE tube into the outlet hole (on the rear of the skeleton) of the flexion tendon (figure 5.37), pass it through the pass-through tunnel and let it come out through the inlet hole on the front of the skeleton and insert it into the initial slot (figure 5.36).
2. Take the remaining part (on the rear of the skeleton) and thread it first through the pass-through tunnel and then into the final slot (figure 5.35).
3. Note: if the tube is too long, shorten it by cutting it with a utility knife.
2. Extension tendon:
1. Insert one end of the PTFE tube into the initial slot (on the rear of the skeleton) of the extension tendon (figure 5.39).
2. Insert the other end into the pass-through tunnel and then into the final slot (figure 5.38).
3. Note: if the tube is too long, shorten it by cutting it with a utility knife.

Figure 5.35 : Inserting the tube into the pass-through tunnel and then into the final slot (rear view); FINAL SLOT; TUNNEL

Figure 5.37 : Inserting the tube into the tendon outlet hole (rear view)

Figure 5.36 : Inserting the tube into the initial slot (front view)

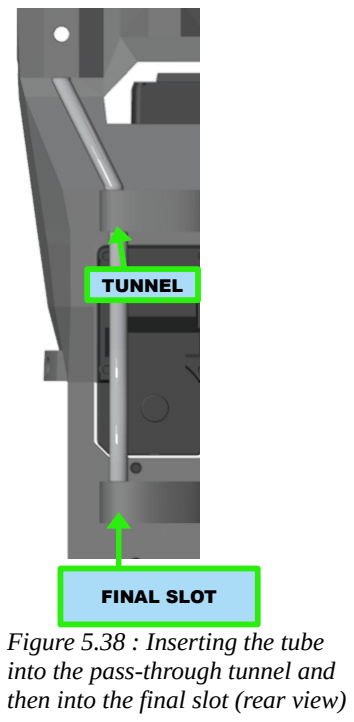
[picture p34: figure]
Figure 5.38 : Inserting the tube into the pass-through tunnel and then into the final slot (rear view); FINAL SLOT; TUNNEL

Figure 5.39 : Inserting the tube into the initial slot (rear view)

5.7.5 Checking the Bowden tube installation
Before proceeding, make sure all the Bowden tubes are correctly installed as shown in the figure.

Figure 5.41: Front view with Bowden tubes installed

Figure 5.40: Rear view with Bowden tubes installed

## 5.8 Inserting tendons into the Bowden tubes (flexion end)

Procedure to be applied only to the tendons of the index, middle, ring, and little fingers.
This operation requires a nylon needle at least 20 cm long (40 cm of unfolded thread).
For each finger:
1. On the front of the skeleton, insert the two ends of the nylon needle into the inlet hole in front of the finger slot (figure 5.43) and push them into the PTFE tube below, bringing them out through the outlet hole on the rear of the skeleton (figure 5.42)
2. Insert the flexion end of the tendon into the loop of the nylon needle left outside the inlet hole (figure 5.43) and pull the ends of the nylon needle from the other end of the Bowden tube until the entire tendon comes out of the outlet hole (figure 5.44).

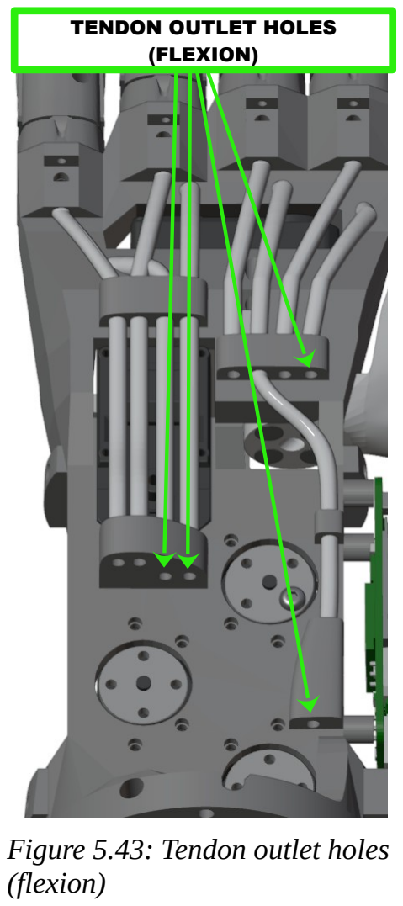
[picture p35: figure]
Figure 5.43: Tendon outlet holes (flexion); TENDON OUTLET HOLES (FLEXION)

Figure 5.42: Tendon inlet holes (flexion)


Figure 5.44: Flexion ends of the tendons emerging from the Bowden tubes

## 5.9 Inserting tendons into the Bowden tubes (extension end)

Procedure to be applied only to the tendons of the index, middle, ring, and little fingers.
This operation requires a nylon needle at least 20 cm long (40 cm of unfolded thread).
For each finger:
3. On the rear of the skeleton: insert the two ends of the nylon needle into the finger's final hole and then into the inlet hole of the Bowden tube below (figure 5.46).
4. Push the nylon threads until they come out of the outlet hole (figure 5.45).
5. Insert the extension end of the tendon into the loop of the nylon needle left outside the finger's final hole (figure 5.46) and pull the ends of the nylon needle from the other end of the Bowden tube until the entire tendon comes out of the outlet hole (figure 5.47)

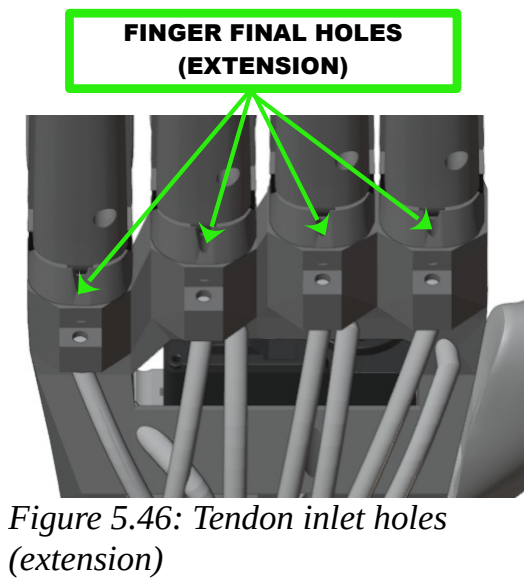
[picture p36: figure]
Figure 5.46: Tendon inlet holes (extension); FINGER FINAL HOLES (EXTENSION)

Figure 5.47: Extension ends of the tendons emerging from the Bowden tubes

## 5.10 Installing tendons on the spools

5.10.1 Safety information
!! DO NOT PULL THE TENDON WITH BARE HANDS !! MANDATORY
- Use a vice to hold the part being worked on firmly in place
- Use assembly pliers to pull the tendon
POSSIBLE HARM:
- Severe cuts to the fingers
- Blood loss

MANDATORY USE OF THE VICE

MANDATORY USE OF THE ASSEMBLY PLIERS

DANGER OF FINGER CUTS

5.10.2 Nylon needle technique
The tendons are thin and difficult to thread, which is why a special needle must be used.
This special needle is actually a length of nylon thread used as if it were a needle.
This method was chosen after multiple trials with various different tools, as it proved to be the fastest, most reliable, and safest.
The procedure for threading the tendon through a hole using a nylon thread (10 cm long, 0.35 mm diameter) as a needle is shown below:

WARNING: the tendons can cut fingers! MANDATORY: use the vice to secure the spool, and the assembly pliers to pull the tendon.

NOTE: Hereafter, this sequence of operations will simply be referred to as "threading the tendon." It is implicitly assumed that this is done using the nylon needle.

Figure 5.48: Threading the ends of the nylon thread, one at a time, through the hole

Figure 5.49: Threading the tendon into the nylon loop

Figure 5.51: pulling with the assembly pliers the shorter part of the tendon through the other side of the hole

Figure 5.50: Pulling with the assembly pliers the two ends of the nylon loop through the other side of the hole

5.10.3 Installing tendons on the spools (index, middle, ring and little fingers)

WARNING: the tendons can
cut fingers!
MANDATORY: use the vice to secure the skeleton, and the assembly pliers to pull the tendon.

5.10.3.1 Preparing the spool assembly
Each servo requires one flexion spool and one extension spool, mounted one above the other. See figure.
For each flexion spool (shown in yellow in figure 5.52):
1. Position the extension spool (shown in blue in figure 5.52)
1. Make sure the flexion spool (yellow in figure 5.52) has its smaller diameter at the bottom.
2. Fixing the extension spool with 4 M3 x 10 mm button-head bolts (figure 5.53): the screws will hold the assembly together temporarily, by simple interlocking, without being tightened (it is important that they remain joined until the end of the next step, 'Installing tendons on the spools').

Figure 5.53: Assembled
spool

Figure 5.52: The bolts
hold the assembly
together

5.10.3.2 Installing tendons on the spools (index, middle, ring and little fingers)
Make sure each spool assembly is correctly assembled (the screws temporarily hold the extension spool joined to the flexion spool by simple interlocking, without being tightened)
Preparation:
1. Make sure all servo motors are connected, and that the spools are not installed.
2. Power the logic board using the power connector (make sure the USB cable is disconnected) as shown in figure 5.54.
3. Connect (BT SERIAL TOOL TO BE PROVIDED) via Bluetooth to the device (device name: YEAH-HAND-X-YYYYYY, where X is 'L' or 'R' depending on the model, and YYYYYY is the serial number)
4. send the 'INSTALL' selection serial command via Bluetooth.
5. wait for the servo motors to complete their movement, then proceed with the following paragraphs:
1. Installing tendons on the spools (index, middle, ring and little fingers)
2. Installing tendons on the spools (thumb)

Figure 5.54: Power
connector inserted

Installing tendons on the spools (index, middle, ring and little fingers):
1. For each servo motor:
1. Identify the corresponding finger (or fingers, for ring and little) and the corresponding spool assembly (the flexion spool and extension spool are currently held together by inserted, but not yet tightened, bolts)
2. Take the flexion end of the tendon (2 ends for ring and little)
3. Thread the end(s) into the bottom-right hole of the flexion spool and pass it out through the corresponding hole of the extension spool (figure 5.56), make sure enough tendon protrudes to prevent it slipping back through.
4. Make sure the spool assembly does not come apart during these operations.
5. Take the extension end of the tendon (2 ends for ring and little)
6. Thread the end(s) into the top hole of the extension spool and pass it out through the bottom hole of the same spool (figure 5.55), make sure enough tendon protrudes to prevent it slipping back through.
7. Position the spool assembly onto its servo motor, with the arrow pointing up (figure 5.28)
8. Screw the spool assembly onto the flange of its servo motor using the M3 bolts
9. Completing the extension end of the tendon:
1. Make the tendon wrap one clockwise turn around the extension spool before it enters the top hole (figure 5.60)
2. Pull the tendon through the bottom hole (until the finger is straight) and wrap it around the left bolt with a clockwise rotation (figure 5.59).
3. While holding the tendon taut with the assembly pliers, firmly tighten the bolt with the wrench to lock the tendon (figure 5.58)
10. Completing the flexion end of the tendon:
1. Pull the tendon until taut, without shifting the position of the controlled finger, and wrap it around the right bolt with a clockwise rotation (figure 5.61).
2. While holding the tendon taut with the assembly pliers, firmly tighten the bolt to lock the tendon (figure 5.62).

Figure 5.56: Inserting the flexion end; INLET HOLE; OUTLET HOLE

Figure 5.55: Inserting
the extension end

Figure 5.57: Spool
assemblies mounted with
arrow pointing up

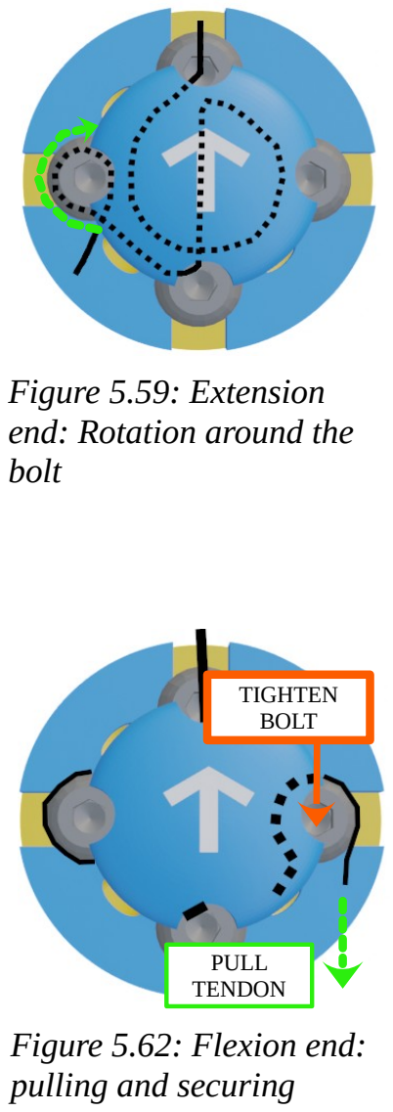
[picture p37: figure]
Figure 5.59: Extension end: Rotation around the bolt; Figure 5.62: Flexion end: pulling and securing; PULL TENDON; TIGHTEN BOLT

Figure 5.61: Flexion end:
Rotation around the bolt

Figure 5.60: Extension end – Pulling and securing; PULL TENDON; TIGHTEN BOLT

Figure 5.58: Pre-winding
operation for the tendon's extension end

Installing tendons on the spools (thumb)
Note: the thumb uses a single spool for both extension and flexion.
1. Only for the thumb servo motor
1. Take the flexion end of the tendon
2. Thread the end into the top right hole of the spool and pass it out through the corresponding outlet hole (figure 5.64), make sure enough tendon protrudes to prevent it slipping back through.
3. Take the extension end of the tendon
4. Thread the end into the bottom left hole of the spool and pass it out through the corresponding outlet hole of the same spool (figure 5.65), make sure enough tendon protrudes to prevent it slipping back through.
5. Position the spool onto its servo motor and secure it with 4 M3 bolts (figure 5.66)
6. Pull the extension end of the tendon through the bottom hole (until the finger is straight) and secure it to the bottom bolt with a clockwise rotation around it (figure 5.67). While holding the tendon taut with the assembly pliers, firmly tighten the bolt to lock the tendon (figure 5.38). Figure 5.63 shows the completed operation.
7. Pull the flexion end of the flexion tendon without shifting the finger's position and secure it to the bolt at the top with a clockwise rotation around it (figure 5.68). While holding the tendon taut with the assembly pliers, firmly tighten the bolt to lock the tendon (figure 5.68). Figure 5.69 shows the completed operation.

Figure 5.64: Thumb spool:

Inserting the extension end Figure 5.63: Thumb spool: Inserting the flexion end

INLET HOLE | OUTLET HOLE

Figure 5.65: Positioning the spool on the servo motor

Figure 5.66: Rotation
around the bolt and securing

Figure 5.67: Tendon
secured under the bolt

Figure 5.69: Rotation
around the bolt

Figure 5.68: Tendon secured under the bolt

## 5.11 Installing the palm

Position the palm and secure it with 4 M2 screws, 6-8mm long (see figure )

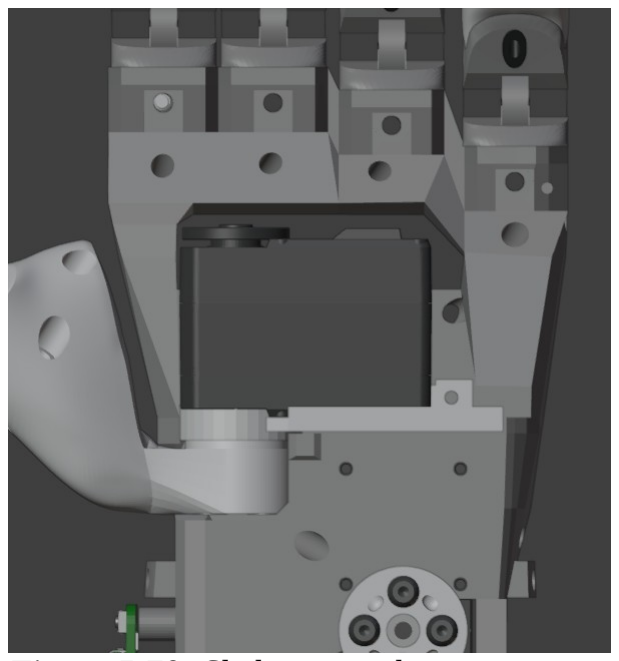
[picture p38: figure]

Figure 5.70: Skeleton - palm area | Figure 5.71: Skeleton - palm installed

## 5.12 Installing the covers

5.12.1 Installing the upper cover
Position the pins on the thumb side into the skeleton holes, snap them into place, then, while rotating the cover, snap the pins on the other side into place (see figures 5.73 and 5.72).

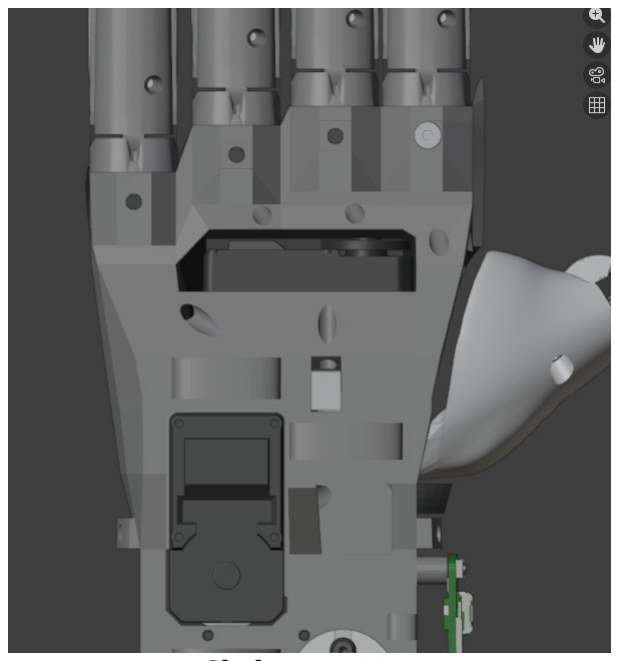
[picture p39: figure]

Figure 5.73: Skeleton - Upper cover area

Figure 5.72: Skeleton - Upper cover installed

5.12.2 Installing the lower covers
1. Make sure the logic board is already mounted on the skeleton
2. Make sure the logic board is connected to the servo motor at the base of the skeleton with the control cable
3. Position the pins on one side of the rear cover onto the corresponding interlocking holes on the skeleton, snap them into place, then, while rotating the cover, snap the pins on the other side into place. See figures 5.74 and 5.75.
4. Position the pins on one side of the front cover onto the corresponding interlocking holes on the skeleton, snap them into place, then, while rotating the cover, snap the pins on the other side into place. See figures 5.76 and 5.77.

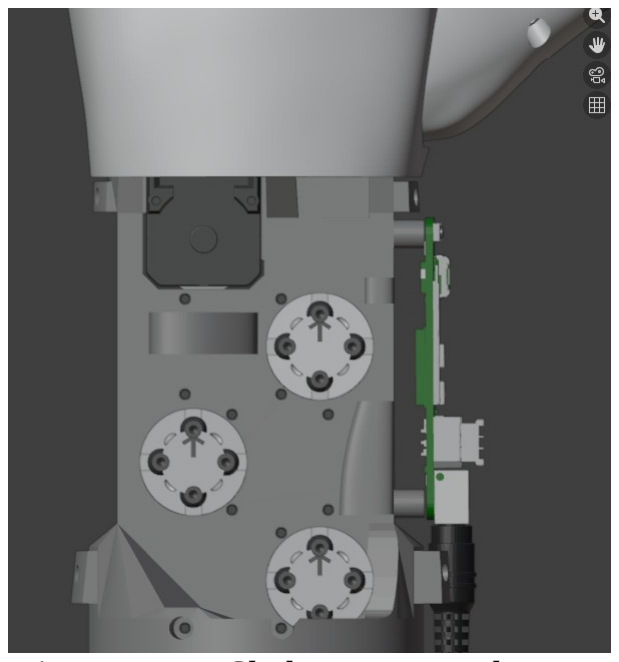
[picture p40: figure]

Figure 5.74: Skeleton - Rear lower cover area

Figure 5.75: Skeleton - Rear lower cover installed

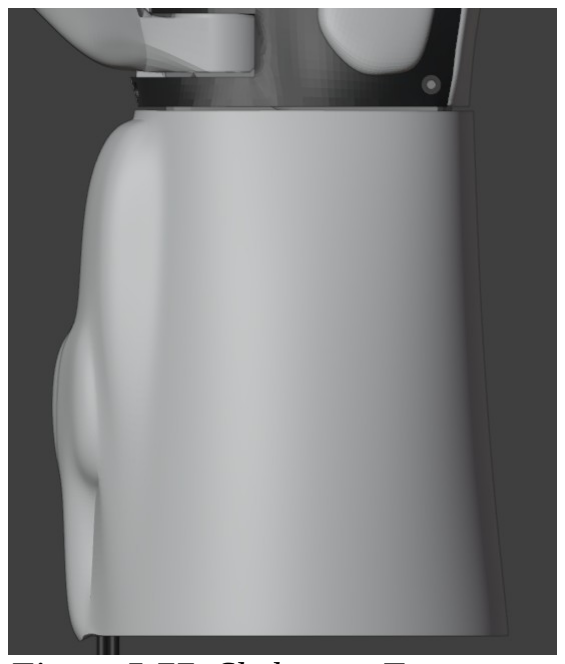
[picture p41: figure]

Figure 5.77: Skeleton - Front lower cover installed

Figure 5.76: Skeleton - Front lower cover area

5.12.3 Installing the finger covers
For each upper finger (index, middle, ring, little)
1. position the distal cover on the distal phalanx and press to snap it into place
2. position the medial cover on the medial phalanx and press to snap it into place
3. position the proximal cover on the proximal phalanx and press to snap it into place

For the thumb:
1. position the distal cover on the distal phalanx and press to snap it into place
2. position the proximal cover on the proximal phalanx and press to snap it into place


Figure 5.78: Finger covers installed

## 6 Installing the robotic hand on a Robotic Manipulator

1. Position the flange on the robot wrist, aligning it with the alignment pin.
2. Tighten with 4 M6 countersunk bolts, 3 cm long. TBD
3. Position the robotic hand on the flange in the desired orientation.
4. Secure with 4 M3 countersunk bolts, 3 cm long. TBD
5. Connect the robotic hand's power cable connector to the robot wrist connector.

The supplied logic board (WaveShare ESP32 Servo Driver Board) requires 12V DC.
If the robotic hand needs to be powered at 24V DC, the voltage conversion board must be installed, which steps the voltage down from 24V to 12V. In that case, a 2A fuse must be used.

USE ONLY POWER SUPPLIES WITH THE FOLLOWING OUTPUT CHARACTERISTICS:
VOLTAGE: 12V DC
2A < CURRENT < 5A

Depending on the available power supply, install the appropriate fuse (see table).

DC power supply | Fuse to install
12V 2A | 2A
12V 4A | 4A
12V 5A | 5A
24V 2A + 12V Conversion Board 4A | 4A
24V 1A + 12V Conversion Board 2A | 2A

TODO INSERT FIGURES OF THE 24/12 CONVERSION BOARD

## 7 Original equipment manufacturer settings

The robotic hand's default settings are as follows:
| • Control mode ◦ Grasp Control ▪ MONKEY GRASP • Finger position: ◦ factor: 0% (maximum opening) • Bluetooth device name: ◦ YeahHand_XXX, where XXX is a unique code.

## 8 Operation

READ THE MANUAL BEFORE USING THE ROBOTIC HAND

READ THE INFORMATION ON TYPICAL OPERATION

## 8.1 Startup

To start the robotic hand, activate power from the controls of the robotic arm on which it is installed, so that the robot wrist connector supplies 12V and at least 162W of power.
The robotic hand begins the tendon auto-calibration phase; once complete, the robotic hand will be in the maximum finger-opening position, in grasping mode: monkey grasp.
Connect to the robotic hand from the robot's control system via a Bluetooth serial character connection (device name: YEAH-HAND-L_XXXXX or YEAH-HAND-R_XXXXX, where XXXXX is the robotic hand's serial number).
Serial commands follow the format CMD X Y ...\r\n, where CMD is the command string and X Y ... are additional parameters, while \r\n is the final send sequence (carriage return and newline)

## Configuration

The following parameters can currently be configured:

Parameter | Command | Variables
PINCH Offset | SETPINCH X\r\n | X: [-40, 40] Pinch Offset
Load Limit | LIM X Y\r\n | X: [1, 5] Motor IDY: [0, 600] Load Limit Value

## 8.2 Selecting the control mode

Control mode | Full command
Monkey grasp | MONKEY\r\n
Power grasp | POWER\r\n
Pinch grasp The PINCH gesture requires configuring the pinch offset via the SETPINCH command, see the relevant paragraph.¹ | PINCH\r\n
Relax | RELAX\r\n
RAW | RAW\r\n

1

## 8.3 Finger movement

8.3.1 Grasp Control mode
If a mode among MONKEY, POWER, POWERSMALL, PINCH has been selected, the robotic hand can be commanded as follows:
- Command: X\r\n
- Meaning: X expresses the integer value [0, 100] representing the percentage of finger closure (each type of selected grasp applies closure to all fingers differently from the other grasps)

Examples:

EXAMPLE | FULL COMMAND
Maximum opening | 0\r\n
Maximum closure | 100\r\n
50% closure | 50\r\n
75% closure | 75\r\n

8.3.2 ROS mode
If the 'ROS' mode has been selected, the robotic hand can be commanded as follows:
- Command: ROS V W X Y Z\r\n
- Meaning:
- ROS : initial data packet tag
- V expresses an integer closure value [0, 100] for index flexion
- W expresses an integer closure value [0, 100] for middle flexion
- X expresses an integer closure value [0, 100] for ring flexion
- Y expresses an integer closure value [0, 100] for thumb flexion
- Z expresses an integer closure value [0, 100] for thumb rotation

Examples:

EXAMPLE | FULL COMMAND
Index flexion: 30%Middle flexion: 50%Ring and little flexion: 10%Thumb flexion: 70%Thumb rotation: 65% | ROS 30 50 10 70 65\r\n
Index flexion: 10%Middle flexion: 20%Ring and little flexion: 30%Thumb flexion: 40%Thumb rotation: 50% | ROS 10 20 30 40 50\r\n
Flexion: maximum openingThumb rotation: maximum opening (open hand) | ROS 0 0 0 0 0\r\n
Flexion: maximum closureThumb rotation: maximum closure (thumb in opposition) | ROS 100 100 100 100 100\r\n

## 9 Changing product or capacity

Before replacing an object gripped by the robotic hand, make sure its characteristics fall within the limits set out in the chapter Technical characteristics of the machine in the section "Object properties".

## 10 Inspections, tests and maintenance

## 10.1 Expected component lifetime

Note: a cycle is one complete closure of the finger from the 0% position (fully open) to the 100% position (fully closed, equal to 300° of servo motor rotation) and subsequent reopening to the 0% position.

COMPONENT | LIFETIME IN CYCLES: values found experimentally with prolonged use of the product (2024-2025-2026 period).²
Skeleton | 200000
TRS Platform | 200000
Thumb base | 20000
Fingers | 20000
Spools | 20000
Covers | 200000
Tendons and Bowden tubes | 200000
Servo motors: calculated based on data from the original manufacturer WaveShare. The ST3215-HS servo motor has a service life of 100000 cycles, where one cycle consists of rotating the flange from 0° to 60° and back to 0°.³ | 20000
Logic board | 200000

## 10.2 Nature, frequency and inspection criteria

COMPONENT | INSPECTION INTERVAL IN CYCLES
Skeleton | 50000
TRS Platform | 50000
Thumb base | 5000
Fingers | 5000
Spools | 5000
Covers | 50000
Tendons and Bowden tubes | 50000

2

3

Servo motors | 5000
Logic board | 50000

## 10.3 Spare parts specifications

All spare parts are specified in the following table:

DESCRIPTION | QTY PER PRODUCT | MANUFACTURER | MODEL
skeleton | 1 | VITTORIO-LUMARE | H-SKELETON-X
index finger with silicone pads | 1 | VITTORIO-LUMARE | H-FING-IF-X
middle finger with silicone pads | 1 | VITTORIO-LUMARE | H-FING-MF-X
ring finger with silicone pads | 1 | VITTORIO-LUMARE | H-FING-RF-X
little finger with silicone pads | 1 | VITTORIO-LUMARE | H-FING-LF-X
thumb with silicone pads | 1 | VITTORIO-LUMARE | H-FING-TF-X
palm with silicone pads | 1 | VITTORIO-LUMARE | H-PALM-X
thumb base | 1 | VITTORIO-LUMARE | H-FING-TB-X
Bowden tubes | 1 | VITTORIO-LUMARE | H-PTFE-TUBING-X
tendon spool | 4 | VITTORIO-LUMARE | H-SPOOL-X
front cover | 1 | VITTORIO-LUMARE | R-COV-F-X
rear cover | 1 | VITTORIO-LUMARE | R-COV-B-X
index finger cover set | 1 | VITTORIO-LUMARE | H-FING-COV-IF-X
middle finger cover set | 1 | VITTORIO-LUMARE | H-FING-COV-MF-X
ring finger cover set | 1 | VITTORIO-LUMARE | H-FING-COV-RF-X
little finger cover set | 1 | VITTORIO-LUMARE | H-FING-COV-LF-X
thumb cover set | 1 | VITTORIO-LUMARE | H-FING-COV-TF-X
UR3 flange | 1 | VITTORIO-LUMARE | R-FLANGE-UR3-X
servo motors and cables | 5 | WAVESHARE | ST3215-HS
logic board | 1 | WAVESHARE | Servo Driver with ESP32
polyethylene tendon (spool) | 1 | HERCULES | 90.7 kg, 0.75mm, 8 strands
M3 bolts, countersunk head, 20 mm long | TBD | N.A. | N.A.
M3 bolts, countersunk head, 16 mm long | TBD | N.A. | N.A.
M3 bolts, countersunk head, 12 mm long | TBD | N.A. | N.A.

M3 bolts, button head, 10 mm long | TBD | N.A. | N.A.
M6 bolts, hex head, 35 mm long | TBD | N.A. | N.A.
M3 bolts, countersunk head, 20 mm long | TBD | N.A. | N.A.
M2 bolts, hex socket head, 5 mm long | TBD | N.A. | N.A.
M2 self-tapping screws, 6mm long | TBD | N.A. | N.A.

## 10.4 Tools and equipment

10.4.1 Assembly and maintenance tools and equipment These are the tools and equipment required for assembly

DESCRIPTION | QTY | MANUFACTURER | MODEL
Long Phillips #1 screwdriver for electronics 6.69" | 1 | WIHA | 261110
Precision pliers 4.72" | 1 | ADAFRUIT INDUSTRIES LLC | 422
Hex screwdriver 2mm 5.71" | 1 | WIHA | 26320
Hex screwdriver 1.5mm 7.05" | 1 | WIHA | 36715
Small assembly pliers | 1 | OLIMEX LTD | CHN-PLI-LC

## 10.5 Energy isolation procedures

To disconnect the electrical power source feeding the robotic hand, it is sufficient to unplug the power plug from the side connector (figure 10.1).

Figure 10.1: Connector with power plug inserted

POWER PLUG

## 10.6 Extraordinary maintenance

These operations are to be performed only when a component requires replacement. 10.6.1 Finger replacement
Perform in sequence:
1. Tendon removal
2. Finger removal
3. Finger installation
4. Tendon installation
5. Tendon registration

10.6.2 Finger removal

USE THE VICE

1. Unscrew all finger fastening bolts
2. Remove all fingers from their slots

10.6.3 Finger installation

USE THE VICE

See Chapter 5.5. Installing the Index, Middle, Ring and Little fingers See Chapter 5.1.5. Installing the Thumb finger

10.6.4 Tendon removal

1. Cut all tendons with scissors
2. Unscrew the tendon fastening bolts from all spools using the 2.5mm hex wrench provided
3. Remove all tendons using the assembly pliers provided

10.6.5 Tendon installation

See Chapter 5.4. Installing the tendons in the fingers

10.6.6 Motor replacement
Perform in sequence:
1. Motor removal
2. Motor installation

10.6.7 Motor removal
1. Remove each servo motor by unscrewing its 4 fastening screws, following this sequence:
1. ring-little finger flexion servo motor
2. index finger flexion servo motor
3. middle finger flexion servo motor
4. thumb flexion servo motor
5. thumb rotation servo motor

10.6.8 Motor installation
See Chapter 5.1. Servo motor installation and registration

10.6.9 Cover replacement
Perform in sequence:

1. Cover removal
2. Cover installation

10.6.10 Cover removal
1. Detach the front snap-fit cover (palm side)
2. Detach the rear snap-fit cover (back side)

10.6.11 Cover installation
See Chapter Installing the covers

10.6.12 Skeleton replacement
To replace the skeleton, all components must be removed and the robotic hand reassembled from the beginning.
Perform in sequence:
1. Cover removal
2. Board removal
3. Tendon removal
4. Bowden tube removal
5. Spool removal
6. Finger removal
7. Servo motor removal, including the TRS Platform
8. SKELETON REPLACEMENT
9. Servo motor installation, including the TRS Platform
10. Finger installation
11. Spool installation
12. Bowden tube installation
13. Tendon installation
14. Board installation
15. Cover installation

## 10.7 Tendon registration

For each finger requiring registration:
1. Secure the robotic hand in the vice
2. connect the servo motor to the SSI slot on the electronic board.
3. power the electronic board with a 12V DC power supply capable of delivering up to 14A, with a unipolar connector with a positive central pin
4. connect to the logic board via Bluetooth.
5. send the 'Tendon Installation Mode' selection serial command via Bluetooth.
6. wait for the servo motors to complete their movement, then proceed to the next step
7. For each finger requiring registration
1. Loosen the extension tendon bolt by 2 turns using the 2.5mm hex wrench
2. Loosen the flexion tendon bolt by 2 turns using the 2.5mm hex wrench
3. Make sure the finger is fully extended; otherwise extend it manually
4. Using the assembly pliers with one hand, take hold of the extension tendon and pull it until taut
5. While keeping the tendon taut with the assembly pliers, with the other hand tighten the fastening bolt until firmly secured (TBD: tightening torque to be defined)
6. Release the tendon from the assembly pliers
7. Make sure the finger is fully extended under the effect of the tendon's tension
8. Using the assembly pliers with one hand, take hold of the flexion tendon and pull it until taut

9. While keeping the tendon taut with the assembly pliers, with the other hand tighten the fastening bolt until firmly secured (TBD: tightening torque to be defined)
10. Release the tendon from the assembly pliers

## 11 Cleaning and disinfection

The external surfaces of the robotic hand may be cleaned with:
- a cloth lightly dampened with alcohol.
- a cloth lightly dampened with a chlorine-based disinfectant (e.g. Amuchina).

DO NOT SPRAY LIQUIDS ONTO THE ROBOTIC HAND
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

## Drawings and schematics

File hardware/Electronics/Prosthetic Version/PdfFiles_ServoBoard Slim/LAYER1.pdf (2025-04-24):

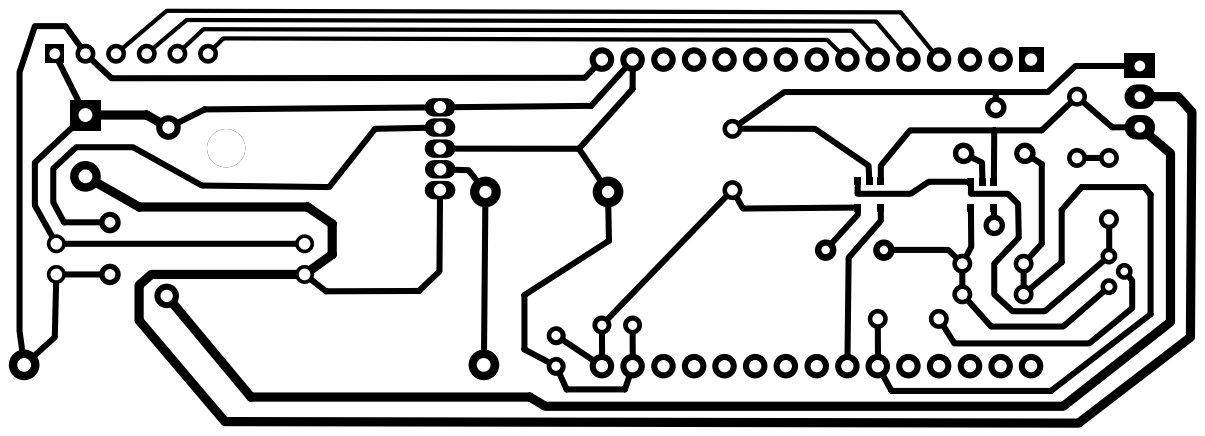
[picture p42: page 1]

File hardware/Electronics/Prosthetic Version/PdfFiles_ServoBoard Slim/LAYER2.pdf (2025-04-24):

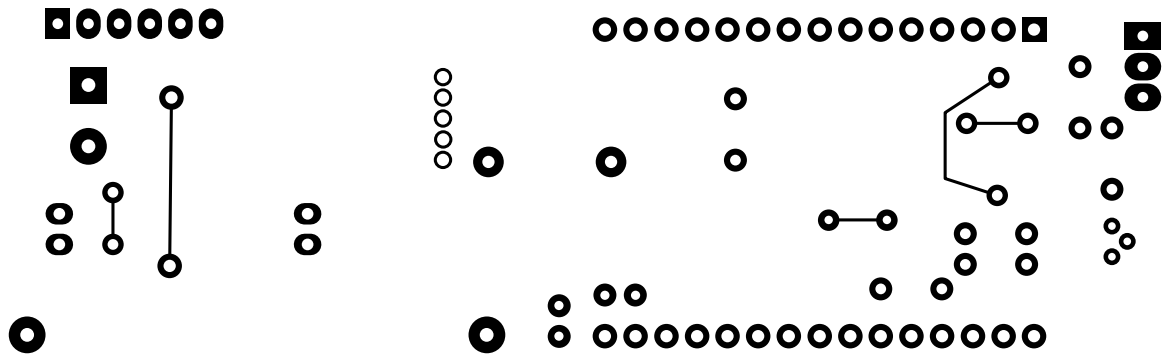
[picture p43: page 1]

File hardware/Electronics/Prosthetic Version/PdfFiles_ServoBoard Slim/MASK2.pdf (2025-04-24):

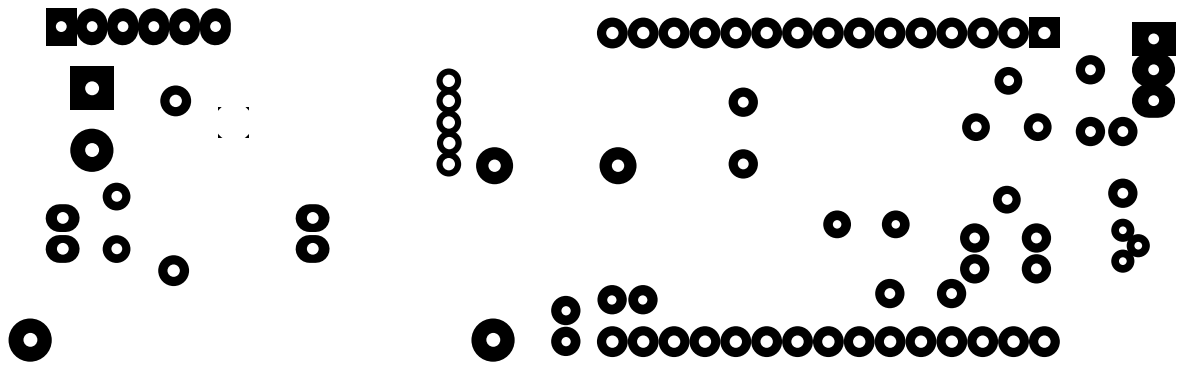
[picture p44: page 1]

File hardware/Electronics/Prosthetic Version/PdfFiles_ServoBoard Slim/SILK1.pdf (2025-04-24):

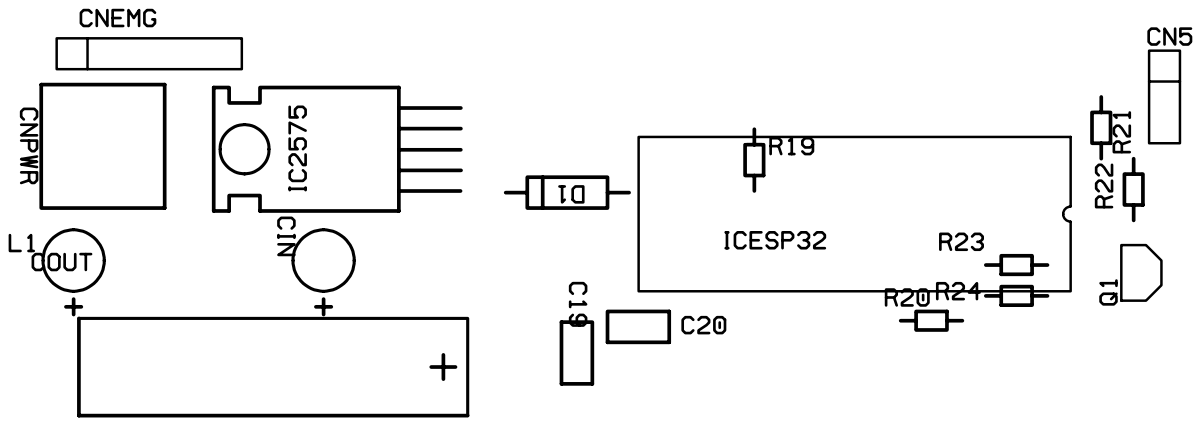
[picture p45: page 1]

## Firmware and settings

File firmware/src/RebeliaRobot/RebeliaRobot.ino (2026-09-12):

/*
Rebelia-Robotic-Firmware is the control software for the Rebelia Robotic Hand, a robotic end-effector device (see https://www.robotgarage.org).

The Copyright Notice
Copyright (C)  2023 Vittorio Lumare

The License Notices
    This file is part of Rebelia-Robotic-Firmware.

    Rebelia-Robotic-Firmware is free software: you can redistribute it and/or modify it under the terms of the GNU General Public License as published by the Free Software Foundation, either version 3 of the License, or (at your option) any later version.

    Rebelia-Robotic-Firmware is distributed in the hope that it will be useful, but WITHOUT ANY WARRANTY; without even the implied warranty of MERCHANTABILITY or FITNESS FOR A PARTICULAR PURPOSE. See the GNU General Public License for more details.

    You should have received a copy of the GNU General Public License along with Rebelia-Hand-Firmware. If not, see <https://www.gnu.org/licenses/>. 
*/

#include <SCServo.h>
#include <BTAddress.h>
#include <BTAdvertisedDevice.h>
#include <BTScan.h>
#include <BluetoothSerial.h>
#include "fingers_controller.h"

#define S_RXD 18
#define S_TXD 19
#define BLUETOOTH true
#define DEBUG false

static const bool SHOW_FEEDBACK = false;
static const bool CALIBRATE_CENTER = false;

BluetoothSerial SerialBT;
SMS_STS st;
FingersController fc(&SerialBT);

void servoIdDiscovery() {
  SerialBT.println("Servo ID Discovery");
  for (int i = 0; i <= 5; i++) {
    int ID = st.Ping(i);
    if (ID != -1) {
      SerialBT.print("Servo ID:");
      SerialBT.println(ID, DEC);
      delay(100);
    } else {
      SerialBT.print("Servo ID:");
      SerialBT.print(ID, DEC);
      SerialBT.println(" ERROR!");
      delay(2000);
    }
  }
}

void setup() {
  Serial.begin(115200);
  SerialBT.begin("YeahHand");
  SerialBT.setTimeout(50);
  //delay(10000);
  SerialBT.println("Yeah Hand Started!");

  // Hand Calibration
  fc.calibrateHand();
}

FingersController::GraspType g_grasp_type = FingersController::GraspType::MONKEY;
FingersController::GraspType g_new_grasp_type = g_grasp_type;
int g_closurePercent = 0;
int g_newClosurePercent = 0;
bool g_preparation = true;
bool g_closure = false;
bool g_motor_enabled[5] = { true, true, true, true, true };
enum class FSM {
  Control,
  TendonInstall,
  Testing,
  DoNothing
};
FSM gFsmState = FSM::Control;

void processStringCmd(const String& cmd);
void prepareGrasp();
void limitLoad();
int sign(int val);

int sign(int val) {
  return val / abs(val);
}

int gMaxOverLoadCount = 40;
int gOverLoadCounters[5];  // 0: index, ..

void processStringCmd(const String& cmd) {
  if (DEBUG) {
    if (BLUETOOTH) SerialBT.printf("string: %s \n", cmd.c_str());
    Serial.print("string: ");
    Serial.println(cmd.c_str());
  }

  FingersController::GraspType graspType = FingersController::getGraspTypeByString(cmd);
  if (graspType < FingersController::GraspType::_MAX) {
    g_new_grasp_type = graspType;
    if (BLUETOOTH) SerialBT.println("Grasp by Serial Cmd");
  } else {  // Not a Grasp command..
    if (cmd.substring(0, 4) == "ROS ") {
      int v[5];
      int n = sscanf(cmd.c_str(), "ROS %d %d %d %d %d",
                     &v[0], &v[1], &v[2], &v[3], &v[4]);
      if (n != 5) {
        // Incomplete line: log and discard
        if (BLUETOOTH && DEBUG) SerialBT.printf("BAD ROS CMD (tokens=%d): %s\n", n, cmd.c_str());
      } else {
        // range check
        for (int i = 0; i < 5; ++i) {
          if (v[i] < 0 || v[i] > 100) {
            if (BLUETOOTH && DEBUG) SerialBT.printf("OUT OF RANGE ROS CMD: %s\n", cmd.c_str());
          } else {
            const u8 IDN = 5;
            FingersController::VectorIdx IDXs[IDN] = { FingersController::VectorIdx::Index, FingersController::VectorIdx::Middle, FingersController::VectorIdx::Ring, FingersController::VectorIdx::Thumb, FingersController::VectorIdx::ThumbRot };
            u8 Factor[IDN] = { v[0], v[1], v[2], v[3], v[4] };
            u16 Speed[IDN] = { 3000, 3000, 3000, 3000, 3000 };
            u8 Acc[IDN] = { 250, 250, 250, 250, 250 };
            fc.moveUntilLoadLimitHit(IDN, IDXs, Factor, Speed, Acc); // sync
            //fc.move(IDN, IDXs, Factor, Speed, Acc); // async
          }
        }
      }
    } else if (cmd.substring(0, 7) == "INSTALL") {
      gFsmState = FSM::TendonInstall;
    } else if (cmd == "TEST\r\n") {
      gFsmState = FSM::Testing;
    } else if (cmd.substring(0, 7) == "CONTROL") {
      gFsmState = FSM::Control;
    } else if (cmd.substring(0, 3) == "LIM") {  // Comando esempio: LIM 1 125
      auto id = cmd.substring(4, 5).toInt();
      auto val = cmd.substring(6, 9).toInt();
      fc.setMaxTorque(id, val);
    } else if (cmd.substring(0, 5) == "INFO ") {
      auto ID = cmd.substring(5, cmd.lastIndexOf('\r')).toInt();
      auto IDX = fc.getVectorIndexByMotorID(ID);
      if (IDX < 0 || IDX > FingersController::SERVOS_SIZE) {
        SerialBT.printf("Wrong ID: %d, ID\n");
        return;
      }
      fc.printFeedback(ID);
      SerialBT.printf("Factor: %d\n", fc.getFactorFromPos(IDX, fc.readPos(ID)));
    } else if (cmd.substring(0, 3) == "POS") {
      u8 IDN = 4;
      u8 IDs[IDN] = { 1, 2, 3, 4 };
      s16 pos[IDN];
      fc.readPositions(IDN, IDs, pos);
      SerialBT.printf("Positions: %d %d %d %d\n", pos[0], pos[1], pos[2], pos[3]);
    } else if (cmd.substring(0, 5) == "MOVE ") {
      int ID = cmd.substring(5, 6).toInt();
      int pos = cmd.substring(6, cmd.lastIndexOf('\r')).toInt();
      fc.moveUntilLoadLimitHit(ID, pos, 2000, 200);
    } else if (cmd.substring(0, 3) == "RT ") {
      int factor = cmd.substring(3, cmd.lastIndexOf('\r')).toInt();
      fc.moveUntilLoadLimitHit(FingersController::VectorIdx::ThumbRot, factor, 3073, 200);
    } else if (cmd.substring(0, 3) == "FI ") {
      int factor = cmd.substring(3, cmd.lastIndexOf('\r')).toInt();
      fc.moveUntilLoadLimitHit(FingersController::VectorIdx::Index, factor, 3073, 200);
    } else if (cmd.substring(0, 3) == "FM ") {
      int factor = cmd.substring(3, cmd.lastIndexOf('\r')).toInt();
      fc.moveUntilLoadLimitHit(FingersController::VectorIdx::Middle, factor, 3073, 200);
    } else if (cmd.substring(0, 3) == "FR ") {
      int factor = cmd.substring(3, cmd.lastIndexOf('\r')).toInt();
      fc.moveUntilLoadLimitHit(FingersController::VectorIdx::Ring, factor, 3073, 200);
    } else if (cmd.substring(0, 3) == "FT ") {
      int factor = cmd.substring(3, cmd.lastIndexOf('\r')).toInt();
      fc.moveUntilLoadLimitHit(FingersController::VectorIdx::Thumb, factor, 3073, 200);
    } else if (cmd.substring(0, 10) == "SETCENTER ") {
      int id = cmd.substring(10, 11).toInt();
      fc.setCenterOfRange(id);
    } else if (cmd.substring(0, 9) == "CALIBRATE") {
      fc.calibrateHand();
    } else if (cmd.substring(0, 9) == "SETPINCH ") {
      int offset = cmd.substring(9, cmd.lastIndexOf('\r')).toInt();
      fc.setPinchOffset(offset);
    } else {
      g_newClosurePercent = cmd.toInt();
      if (BLUETOOTH) SerialBT.printf("ClosurePercent by Serial Cmd: %d\n", g_newClosurePercent);
    }
  }
}

void prepareGrasp() {

  if (g_grasp_type < FingersController::GraspType::_MAX) {
    fc.prepareGrasp(g_grasp_type);
  }
  g_preparation = false;
}

void sendRosFeedback() {
  u8 factors[FingersController::SERVOS_SIZE];
  s16 load[FingersController::SERVOS_SIZE];
  u8 volt[FingersController::SERVOS_SIZE];
  u8 temp[FingersController::SERVOS_SIZE];
  s16 ampr[FingersController::SERVOS_SIZE];
  fc.readFactors(factors);
  fc.readFeedback(load, volt, temp, ampr);
  SerialBT.printf("ROSPOS %d %d %d %d %d\n", factors[0], factors[1], factors[2], factors[3], factors[4]);
  SerialBT.printf("ROSLOAD %d %d %d %d %d\n", load[0], load[1], load[2], load[3], load[4]);
  SerialBT.printf("ROSVOLT %d %d %d %d %d\n", volt[0], volt[1], volt[2], volt[3], volt[4]);
  SerialBT.printf("ROSTEMP %d %d %d %d %d\n", temp[0], temp[1], temp[2], temp[3], temp[4]);
  SerialBT.printf("ROSAMPR %d %d %d %d %d\n", ampr[0], ampr[1], ampr[2], ampr[3], ampr[4]);
}

void smartReadSerialBT() {
  String lastPosCmd = "";
  while (SerialBT.available()) {
    String cmd = SerialBT.readStringUntil('\n');
    if (cmd.length() == 0) continue;
    if (cmd.substring(0, 4) == "ROS ") {
      lastPosCmd = cmd;
    } else {
      processStringCmd(cmd);
    }
  }
  if (lastPosCmd.length() > 0) {
    processStringCmd(lastPosCmd);
  }
}

void loop() {
  auto t0 = millis();

  smartReadSerialBT();

  if (gFsmState == FSM::Control) {
    if (g_new_grasp_type != g_grasp_type) {
      auto full_cmd = FingersController::getGraspStringByType(g_new_grasp_type);
      auto reduced_cmd = full_cmd.substring(0, full_cmd.length() - 2);
      String msg = reduced_cmd + " GRASP ENABLED";

      if (BLUETOOTH) SerialBT.println(msg);

      g_preparation = true;
      g_closure = false;
      g_grasp_type = g_new_grasp_type;
    }

    if (g_newClosurePercent != g_closurePercent) {

      g_preparation = false;
      g_closure = true;
      g_closurePercent = g_newClosurePercent;
    }

    if (g_preparation) {
      prepareGrasp();
    }

    if (g_closure) {
      fc.action(g_grasp_type, g_closurePercent);
      g_closure = false;
    }

  } else if (gFsmState == FSM::TendonInstall) {

    SerialBT.println("Tendon Install..");
    fc.tendonInstallation();
    SerialBT.println("Please install tendons.");

  } else if (gFsmState == FSM::Testing) {
    // test();
  } else if (gFsmState == FSM::DoNothing) {
    delay(10);
  }

  static auto t_prev_ros_feedback = millis();
  auto t_now_ros_feedback = millis();
  if (t_now_ros_feedback - t_prev_ros_feedback > 100) {
    sendRosFeedback();
    t_prev_ros_feedback = t_now_ros_feedback;
  }

  static auto t_safety = millis();
  if (millis() - t_safety > 1000) {
    fc.safetyFeature();
    t_safety = millis();
  }

  static long t_prev_loop = micros();
  long t_cur_loop = micros();
  while (micros() - t_prev_loop < 100)
    ;
  long t_loop_delta = micros() - t_prev_loop;
  t_prev_loop = t_cur_loop;
}

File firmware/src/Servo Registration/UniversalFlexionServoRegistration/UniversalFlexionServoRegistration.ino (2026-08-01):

#include <SCServo.h>
#include "BluetoothSerial.h"

#define S_RXD 18
#define S_TXD 19

SMS_STS st;
int ID_ChangeFrom = 1;  // Change the original servo ID, and the factory default is 1
int ID_ChangeTo = -1;   // IndexFlexionServo: ID 1
int ans = -100;
BluetoothSerial SerialBT;

void pressEnterWhenReady(bool continuous_print = true) {
  SerialBT.println("Press ENTER when ready!"); 
  auto ready = false;
  while (!ready) {
    if (continuous_print) { SerialBT.println("Press ENTER when ready!"); }
    delay(1000);
    if (SerialBT.available()) {
      SerialBT.readStringUntil('\n');
      ready = true;
    }
  }
}

void setup() {
  SerialBT.begin("YeahHand");
  SerialBT.setTimeout(50);
  Serial1.begin(1000000, SERIAL_8N1, S_RXD, S_TXD);
  st.pSerial = &Serial1;
  while (!Serial1) { delay(100); }

  delay(1000);

  pressEnterWhenReady();

  SerialBT.println("\n\nWARNING: This program will modify the ID of the connected servo and will configure its center of range to the current position!");
  SerialBT.println("WARNING: Connect only one servomotor to the logic board!");

  while (ID_ChangeTo < 1) {
    SerialBT.println("Which servo ID do you want to register?");

    while (!SerialBT.available())
      ;

    String cmd = SerialBT.readStringUntil('\n');
    if (cmd.length() > 0) {
      ID_ChangeTo = cmd.toInt();
      if (ID_ChangeTo < 1) {
        SerialBT.println("Please enter an ID > 0..");
      }
    }
  }

  // Identify ID..
  SerialBT.printf("Identifying Servo ID \n");
  SerialBT.printf("Trying with ID %d..", ID_ChangeFrom);
  int retrievedID = st.Ping(ID_ChangeFrom);
  SerialBT.printf("..retrieved: %d\n", ID_ChangeFrom);
  while (retrievedID != ID_ChangeFrom) {
    delay(1000);
    ID_ChangeFrom += 1;
    SerialBT.printf("Trying with ID %d..", ID_ChangeFrom);
    retrievedID = st.Ping(ID_ChangeFrom);
    SerialBT.printf("..retrieved: %d\n", retrievedID);
  }
  // ID identified
  SerialBT.printf("Found ID %d\n", ID_ChangeFrom);

  SerialBT.printf("Programming new ID %d...\n", ID_ChangeTo);
  ans = st.unLockEprom(ID_ChangeFrom);  //Unlock EPROM-SSAFE
  SerialBT.printf("Unlock ID %d, answer: %d\n", ID_ChangeFrom, ans);

  ans = st.writeByte(ID_ChangeFrom, SMS_STS_ID, ID_ChangeTo);  //Change ID
  SerialBT.printf("WriteByte ID %d, answer: %d\n", ID_ChangeFrom, ans);

  ans = st.LockEprom(ID_ChangeTo);  // EPROM-SAFE is locked
  SerialBT.printf("Lock ID %d, answer: %d\n", ID_ChangeTo, ans);

  delay(1000);

  // Check programmed ID
  SerialBT.printf("Trying with ID %d..", ID_ChangeTo);
  retrievedID = st.Ping(ID_ChangeTo);
  SerialBT.printf("..retrieved: %d\n", retrievedID);
  delay(1000);
  if (retrievedID == ID_ChangeTo) {
    SerialBT.printf("Retrieved ID after programming: %d\n", retrievedID);
    SerialBT.printf("REGISTRATION CONFIRMED, NEW ID : %d\n", retrievedID);
  } else {
    SerialBT.printf("ID progamming failed!\n");
    return;
  }

  // Set center of range
  SerialBT.println("\nPlease MANUALLY MOVE the servomotor's FLANGE PLATE to the CENTER OF RANGE position (please check on the instructions manual!)");

  pressEnterWhenReady(false);

  SerialBT.printf("Setting center of range..\n");

  int result = st.CalibrationOfs(ID_ChangeTo);
  delay(1000);
  if (result == 1) {  //Ack 1:Successful 0:Error
    SerialBT.println("Successfully calibrated center of range! ");
  } else {
    SerialBT.printf("Failed center of range calibration! Error: %d\n", result);
  }

  // oscillate servo to confirm its all done
  for (int i = 0; i < 5; i++) {
    st.WritePosEx(ID_ChangeTo, 1948, 1500, 50);  //To control the servo with ID 1, rotate it to position 1000 at a speed of 1500, with a start-stop acceleration of 50.
    delay(400);                                  //[(P1-P0)/V]*1000+100

    st.WritePosEx(ID_ChangeTo, 2148, 1500, 50);  // To control the servo with ID 1, rotate it to position 20 at a speed of 1500, with a start-stop acceleration of 50.
    delay(400);                                  //[(P1-P0)/V]*1000+100
  }
  // Finally move at center of range
  st.WritePosEx(ID_ChangeTo, 2048, 1500, 50);  // To control the servo with ID 1, rotate it to position 20 at a speed of 1500, with a start-stop acceleration of 50.

  SerialBT.printf("Servo ID %d registered! \n Center of range set!\n", ID_ChangeTo);
  SerialBT.println("Please disconnect any servo from the logic board!");
}

void loop() {
  delay(1000);
}

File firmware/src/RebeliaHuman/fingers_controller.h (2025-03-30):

#include <stdexcept>
/*
  Rebelia-Hand-Firmware is the control software for the Rebelia Hand

  Website: https://www.robotgarage.org
  Author: Vittorio Lumare
  Email: vittorio.lumar@robotgarage.org 

  GNU GPL License

  Copyright (c) 2025 Vittorio Lumare

  
  This file is part of Rebelia-Hand-Firmware.

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
  See the GNU General Public License for more details.

  You should have received a copy of the GNU General Public License along 
  with Rebelia-Hand-Firmware. If not, see <https://www.gnu.org/licenses/>. 
*/

#include <SCServo.h>
#include "BluetoothSerial.h"

#include <vector>

// the uart used to control servos.
// GPIO 18 - S_RXD, GPIO 19 - S_TXD, as default.
#define S_RXD 18
#define S_TXD 19

static int limit(const int val, const int a, const int b) {

  if (a <= b) {
    return constrain(val, a, b);
  } else
    return constrain(val, b, a);
}

class FingersController {
public:
  enum GraspType {
    POWER = 0,
    POWERSMALL,
    MONKEY,
    PINCH,
    RELAX,
    _MAX
  };

public:
  static GraspType getGraspTypeByString(const String& cmd) {
    if (cmd == "POWER\r\n") {
      return FingersController::GraspType::POWER;
    } else if (cmd == "POWERSMALL\r\n") {
      return FingersController::GraspType::POWERSMALL;
    } else if (cmd == "MONKEY\r\n") {
      return FingersController::GraspType::MONKEY;
    } else if (cmd == "PINCH\r\n") {
      return FingersController::GraspType::PINCH;
    } else if (cmd == "RELAX\r\n") {
      return FingersController::GraspType::RELAX;
    }

    return FingersController::GraspType::_MAX;
  }



  static String getGraspStringByType(FingersController::GraspType type) {

    String text;

    switch (type) {
      case FingersController::GraspType::POWER:
        text = "POWER\r\n";
        break;
      case FingersController::GraspType::POWERSMALL:
        text = "POWERSMALL\r\n";
        break;
      case FingersController::GraspType::MONKEY:
        text = "MONKEY\r\n";
        break;
      case FingersController::GraspType::PINCH:
        text = "PINCH\r\n";
        break;
      case FingersController::GraspType::RELAX:
        text = "RELAX\r\n";
        break;
      case FingersController::GraspType::_MAX:
        text = "INVALID_COMMAND\r\n";
        break;
    }

    return text;
  }

  void enableTorque(int ID, bool enable) {
    st.EnableTorque(ID, enable);
  }

public:
  FingersController() {
    Serial1.begin(1000000, SERIAL_8N1, S_RXD, S_TXD);
    st.pSerial = &Serial1;

    //      SerialBT.begin();
  }

  // EXAMPLE: st.RegWritePosEx(5, 2150, 3400, 50);//servo(ID1) speed=3400，acc=50，move to position=4095.
public:

  void calibrate(int motor_id) {
    st.CalibrationOfs(motor_id);
  }

  GraspType getGraspTypeByThumbRot() {

    auto pos = getPos(THUMB_ROT_MOTOR);
    if (abs(pos - POWER_THUMB_ROT.front()) < 50) {
      return FingersController::GraspType::POWER;
    } else if (abs(pos - POWERSMALL_THUMB_ROT.front()) < 100) {
      return FingersController::GraspType::POWERSMALL;
    } else if (abs(pos - MONKEY_THUMB_ROT.front()) < 100) {
      return FingersController::GraspType::MONKEY;
    } else if (abs(pos - PINCH_THUMB_ROT.front()) < 100) {
      return FingersController::GraspType::PINCH;
    } else if (abs(pos - RELAX_THUMB_ROT.front()) < 100) {
      return FingersController::GraspType::RELAX;
    }

    return FingersController::GraspType::_MAX;
  }

  void preparePowerGrasp() {

    st.RegWritePosEx(THUMB_FLEX_MOTOR, POWER_THUMB.front(), 3400, 50);
    st.RegWriteAction();
    delay(500);

    st.RegWritePosEx(INDEX_FLEX_MOTOR, POWER_INDEX.front(), 3400, 50);
    st.RegWritePosEx(MIDDLE_FLEX_MOTOR, POWER_MIDDLE.front(), 3400, 50);
    st.RegWritePosEx(RING_LITTLE_FLEX_MOTOR, POWER_RING.front(), 3400, 50);
    st.RegWriteAction();
    delay(500);

    st.RegWritePosEx(THUMB_ROT_MOTOR, POWER_THUMB_ROT.front(), 3400, 50);
    st.RegWriteAction();
    delay(500);
  }

  void powerGrasp(const int factor) {

    byte ID[] = { INDEX_FLEX_MOTOR, MIDDLE_FLEX_MOTOR, RING_LITTLE_FLEX_MOTOR, THUMB_FLEX_MOTOR };
    u16 Speed[] = { 3400, 3400, 3400, 3400 };
    byte ACC[] = { 50, 50, 50, 50 };

    auto index_flex_joint_pos_value = map(factor, 0, 100, POWER_INDEX.front(), POWER_INDEX.back());
    index_flex_joint_pos_value = limit(index_flex_joint_pos_value, POWER_INDEX.front(), POWER_INDEX.back());

    auto middle_flex_joint_pos_value = map(factor, 0, 100, POWER_MIDDLE.front(), POWER_MIDDLE.back());
    middle_flex_joint_pos_value = limit(middle_flex_joint_pos_value, POWER_MIDDLE.front(), POWER_MIDDLE.back());

    auto ring_little_flex_joint_pos_value = map(factor, 0, 100, POWER_RING.front(), POWER_RING.back());
    ring_little_flex_joint_pos_value = limit(ring_little_flex_joint_pos_value, POWER_RING.front(), POWER_RING.back());

    auto thumb_flex_joint_pos_value = map(factor, 0, 30, POWER_THUMB.front(), POWER_THUMB.back());
    thumb_flex_joint_pos_value = limit(thumb_flex_joint_pos_value, POWER_THUMB.front(), POWER_THUMB.back());

    s16 Position[] = { index_flex_joint_pos_value, middle_flex_joint_pos_value, ring_little_flex_joint_pos_value,
                       thumb_flex_joint_pos_value };

    //auto t1 = micros();
    st.SyncWritePosEx(ID, 4, Position, Speed, ACC);  //servo(ID1/ID2) speed=3400, acc=50, move to position=3000.
    //auto t2 = micros();
    //auto dt = (t2 - t1) * 1.0 / 1000.0;
    //SerialBT.printf("SyncWritePosEx [ms]:  %f \n", dt);
    //SerialBT.printf("I%d \tM%d \tR%d \tT%d \n", index_flex_joint_pos_value, middle_flex_joint_pos_value, ring_little_flex_joint_pos_value, thumb_flex_joint_pos_value);
  }

  void preparePowerSmallGrasp() {

    st.RegWritePosEx(THUMB_FLEX_MOTOR, POWERSMALL_THUMB.front(), 3400, 50);
    st.RegWriteAction();
    delay(500);

    st.RegWritePosEx(INDEX_FLEX_MOTOR, POWERSMALL_INDEX.front(), 3400, 50);
    st.RegWritePosEx(MIDDLE_FLEX_MOTOR, POWERSMALL_MIDDLE.front(), 3400, 50);
    st.RegWritePosEx(RING_LITTLE_FLEX_MOTOR, POWERSMALL_RING.front(), 3400, 50);
    st.RegWriteAction();
    delay(500);

    st.RegWritePosEx(THUMB_ROT_MOTOR, POWERSMALL_THUMB_ROT.front(), 3400, 50);
    st.RegWriteAction();
    delay(500);
  }

  void powerSmallGrasp(const int factor) {

    byte ID[] = { INDEX_FLEX_MOTOR, MIDDLE_FLEX_MOTOR, RING_LITTLE_FLEX_MOTOR, THUMB_FLEX_MOTOR };
    u16 Speed[] = { 3400, 3400, 3400, 3400 };
    byte ACC[] = { 50, 50, 50, 50 };

    auto index_flex_joint_pos_value = map(factor, 0, 70, POWERSMALL_INDEX.front(), POWERSMALL_INDEX.back());
    index_flex_joint_pos_value = limit(index_flex_joint_pos_value, POWERSMALL_INDEX.front(), POWERSMALL_INDEX.back());

    auto middle_flex_joint_pos_value = map(factor, 0, 70, POWERSMALL_MIDDLE.front(), POWERSMALL_MIDDLE.back());
    middle_flex_joint_pos_value = limit(middle_flex_joint_pos_value, POWERSMALL_MIDDLE.front(), POWERSMALL_MIDDLE.back());
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

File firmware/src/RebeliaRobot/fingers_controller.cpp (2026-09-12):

/*
Rebelia-Hand-Firmware is the control software for the Rebelia Hand, an Active Prosthetic Hand device (see https://www.robotgarage.org).

The Copyright Notice
Copyright (C)  2023 Vittorio Lumare

The License Notices
    This file is part of Rebelia-Hand-Firmware.

    Rebelia-Hand-Firmware is free software: you can redistribute it and/or modify it under the terms of the GNU General Public License as published by the Free Software Foundation, either version 3 of the License, or (at your option) any later version.

    Rebelia-Hand-Firmware is distributed in the hope that it will be useful, but WITHOUT ANY WARRANTY; without even the implied warranty of MERCHANTABILITY or FITNESS FOR A PARTICULAR PURPOSE. See the GNU General Public License for more details.

    You should have received a copy of the GNU General Public License along with Rebelia-Hand-Firmware. If not, see <https://www.gnu.org/licenses/>. 
*/

#include "fingers_controller.h"

using namespace std::placeholders;

FingersController::GraspType FingersController::getGraspTypeByString(const String& cmd) {
  if (cmd.substring(0, 5) == "POWER") {
    return FingersController::GraspType::POWER;
  } else if (cmd.substring(0, 9) == "POWERTOOL") {
    return FingersController::GraspType::POWERTOOL;
  } else if (cmd.substring(0, 6) == "MONKEY") {
    return FingersController::GraspType::MONKEY;
  } else if (cmd.substring(0, 5) == "PINCH") {
    return FingersController::GraspType::PINCH;
  }

  return FingersController::GraspType::_MAX;
}

String FingersController::getGraspStringByType(FingersController::GraspType type) {

  String text;

  switch (type) {
    case FingersController::GraspType::POWER:
      text = "POWER\r\n";
      break;
    case FingersController::GraspType::POWERTOOL:
      text = "POWERTOOL\r\n";
      break;
    case FingersController::GraspType::MONKEY:
      text = "MONKEY\r\n";
      break;
    case FingersController::GraspType::PINCH:
      text = "PINCH\r\n";
      break;
    case FingersController::GraspType::_MAX:
      text = "INVALID_COMMAND\r\n";
      break;
  }

  return text;
}

void FingersController::enableTorque(u8 ID, bool enable) {
  st.EnableTorque(ID, enable);
}

FingersController::FingersController(BluetoothSerial* _serialBT)
  : SerialBT(_serialBT) {
  Serial1.begin(1000000, SERIAL_8N1, S_RXD, S_TXD);
  st.pSerial = &Serial1;
  while (!Serial1) {
    SerialBT->println("ST3215 serial Not ready");
    delay(100);
  }
  SerialBT->println("ST3215 serial Ready!");
}

FingersController::~FingersController() {
}

void FingersController::tendonInstallation() {
  for (int IDX = VectorIdx::Index; IDX <= VectorIdx::Thumb; IDX++) {
    int ID = getMotorIdByVectorIndex((VectorIdx)IDX);
    switch (hand_side) {
      case HandSide::LeftSide:
        moveUntilLoadLimitHit(ID, LS_MOTORS_POS_TENDON_INSTALLATION[IDX], 2000, 50);
        break;
      case HandSide::RightSide:
        moveUntilLoadLimitHit(ID, RS_MOTORS_POS_TENDON_INSTALLATION[IDX], 2000, 50);
        break;
    }
  }
}

void FingersController::setCenterOfRange(int motor_id) {
  int result = st.CalibrationOfs(motor_id);
  if (result == 0) {
    SerialBT->println("Successfully calibrated center of range! ");
  } else {
    SerialBT->printf("Failed center of range calibration! Error: %d\n", result);
  }
}

void FingersController::setPinchOffset(int offset) {
  if (abs(offset) > 40) {
    SerialBT->println("Please set a value between -40 and 40\n");
    return;
  }
  for (int i = 0; i < PINCH_FRAMES; i++) {
    PINCH_MATRIX[i][VectorIdx::Thumb] = PINCH_GRASP_THUMB_FLEXION + offset;
  }
  SerialBT->printf("Pinch grasp offset: %d\n", offset);
}

void FingersController::calibrateHand() {

  u8 IDN = 5;
  u8 IDN_Flex = 4;
  VectorIdx IDXs[IDN] = { VectorIdx::Index, VectorIdx::Middle, VectorIdx::Ring, VectorIdx::Thumb, VectorIdx::ThumbRot };
  u8 IDs[IDN] = { INDEX_ID, MIDDLE_ID, RING_ID, THUMB_ID, THUMB_R_ID };

  // LeftSide
  s16 LS_START_POS_FOR_OPENING[IDN] = { 1000, 1000, 1000, 1200, 2048 };
  s16 LS_START_POS_FOR_CLOSING[IDN] = { 2500, 2500, 2500, 1200, 2048 };
  s16 LS_END_POS_FOR_OPENING[IDN] = { 50, 50, 50, 50, 50 };
  s16 LS_END_POS_FOR_CLOSING[IDN] = { 4045, 4045, 4045, 4045, 4045 };
  s16 LS_THUMB_FLEXION_START_POS = 50;
  s16 LS_THUMB_ROTATION_START_POS = 50;
  s16 LS_THUMB_ROTATION_END_POS = 4045;
  s16 LS_FLEXION_INCREMENT = 270;
  s16 LS_THUMB_ROT_INCREMENT = 100;

  // RightSide
  s16 RS_START_POS_FOR_OPENING[IDN] = { 3000, 3000, 3000, 2800, 2048 };
  s16 RS_START_POS_FOR_CLOSING[IDN] = { 1500, 1500, 1500, 2800, 2048 };
  s16 RS_END_POS_FOR_OPENING[IDN] = { 4045, 4045, 4045, 4045, 4045 };
  s16 RS_END_POS_FOR_CLOSING[IDN] = { 50, 50, 50, 50, 50 };
  s16 RS_THUMB_FLEXION_START_POS = 4045;
  s16 RS_THUMB_ROTATION_START_POS = 4045;
  s16 RS_THUMB_ROTATION_END_POS = 50;
  s16 RS_FLEXION_INCREMENT = -270;
  s16 RS_THUMB_ROT_INCREMENT = -100;

  // Assign values by Hand Side
  s16 START_POS_FOR_OPENING[IDN];
  s16 START_POS_FOR_CLOSING[IDN];
  s16 END_POS_FOR_OPENING[IDN];
  s16 END_POS_FOR_CLOSING[IDN];
  int THUMB_FLEXION_START_POS;
  int THUMB_ROTATION_START_POS;
  int THUMB_ROTATION_END_POS;
  int FLEXION_INCREMENT;
  int THUMB_ROT_INCREMENT;
  switch (hand_side) {
    case HandSide::LeftSide:
      {
        for (int idx = 0; idx < IDN; idx++) {
          START_POS_FOR_OPENING[idx] = LS_START_POS_FOR_OPENING[idx];
          START_POS_FOR_CLOSING[idx] = LS_START_POS_FOR_CLOSING[idx];
          END_POS_FOR_OPENING[idx] = LS_END_POS_FOR_OPENING[idx];
          END_POS_FOR_CLOSING[idx] = LS_END_POS_FOR_CLOSING[idx];
        }
        THUMB_FLEXION_START_POS = LS_THUMB_FLEXION_START_POS;
        THUMB_ROTATION_START_POS = LS_THUMB_ROTATION_START_POS;
        THUMB_ROTATION_END_POS = LS_THUMB_ROTATION_END_POS;
        FLEXION_INCREMENT = LS_FLEXION_INCREMENT;
        THUMB_ROT_INCREMENT = LS_THUMB_ROT_INCREMENT;
        break;
      }
    case HandSide::RightSide:
      {
        for (int idx = 0; idx < IDN; idx++) {
          START_POS_FOR_OPENING[idx] = RS_START_POS_FOR_OPENING[idx];
          START_POS_FOR_CLOSING[idx] = RS_START_POS_FOR_CLOSING[idx];
          END_POS_FOR_OPENING[idx] = RS_END_POS_FOR_OPENING[idx];
          END_POS_FOR_CLOSING[idx] = RS_END_POS_FOR_CLOSING[idx];
        }
        THUMB_FLEXION_START_POS = RS_THUMB_FLEXION_START_POS;
        THUMB_ROTATION_START_POS = RS_THUMB_ROTATION_START_POS;
        THUMB_ROTATION_END_POS = RS_THUMB_ROTATION_END_POS;
        FLEXION_INCREMENT = RS_FLEXION_INCREMENT;
        THUMB_ROT_INCREMENT = RS_THUMB_ROT_INCREMENT;
        break;
      }
  }

  u16 Speed[IDN] = { 3000, 3000, 3000, 3000, 3000 };
  u8 Acc[IDN] = { 250, 250, 250, 250, 250 };
 
  //waitKeyPress("Pre-position fingers for opening");
  // Pre-position fingers for opening
  setMaxTorque(IDN, IDs, (u16[]){ 250, 250, 250, 250, 250 });
  moveUntilLoadLimitHit(IDN, IDs, START_POS_FOR_OPENING, Speed, Acc);
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

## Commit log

2025-03-03 Added CAD files and renders
    [Hand Back Cover.stl, Index Flex.stl, Index Rigid.stl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]
2025-03-30 Updated license comments in the readme, moved stl files in a folder, added Blender Original Project files
    [Hand Back Cover.stl, Index Flex.stl, Index Rigid.stl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]
2025-04-20 Update BOM.md (connectors)
2025-04-20 Update BOM.md (ESP IC model)
2025-04-20 Added Electronics Board project files
    [SPASTE1.GBR, SPASTE2.GBR, ServoBoardSlim.GBL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]
2025-04-20 Update Readme.txt (updated readme for electronic board)
2025-04-23 Added screenshot of the prosthetic circuit board
2025-11-26 added spool blender file
    [Spools.blend]
2025-11-26 added hierarchic blender file
    [Rebelia - Hierarchic.blend]
2026-02-01 Refactored Fingerscontroller class
2026-03-06 updated CAD files
    [Rebelia - Hierarchic.blend, Spools.blend]
2026-05-10 Updated Blender project and STL files
    [Spools.blend]
